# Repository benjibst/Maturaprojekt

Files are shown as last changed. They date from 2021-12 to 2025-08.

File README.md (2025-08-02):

# Maturaprojekt

A machine that uses image processing to find magnetic objects and automatically remove them from an area.

https://github.com/user-attachments/assets/88520221-f3bb-43c3-997b-82101137d2bb

The magnetic objects might look something like this, they are iron washers with a piece of coloured paper attached to them: <br />
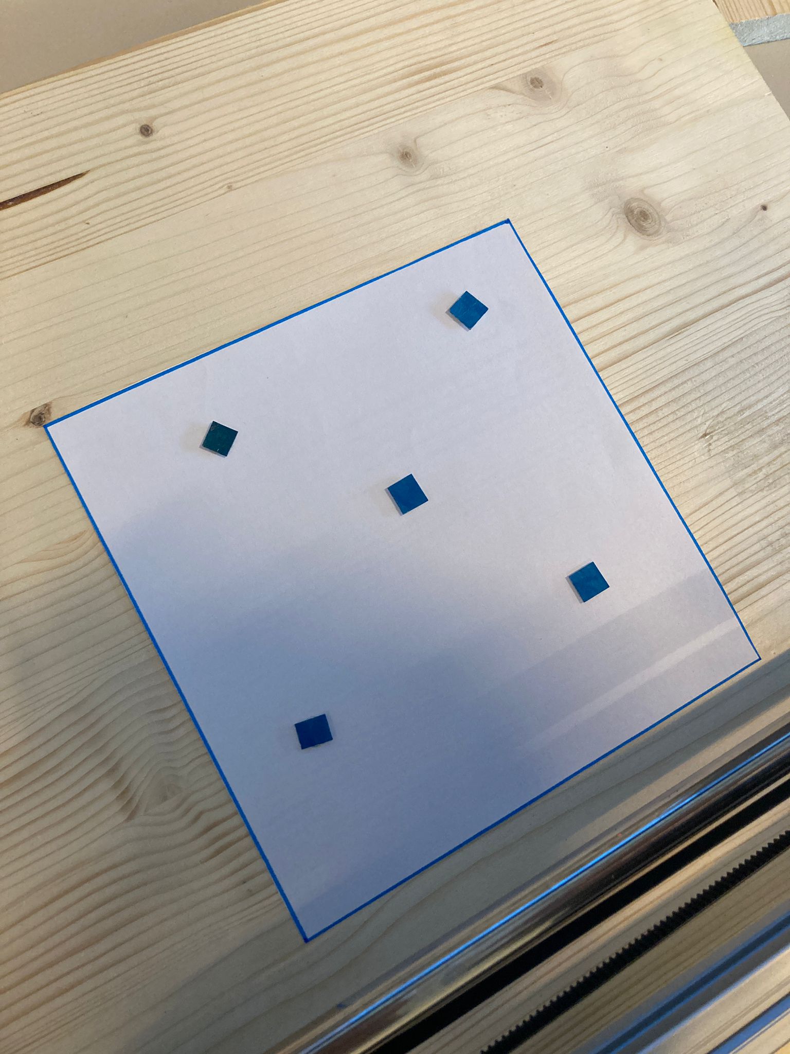
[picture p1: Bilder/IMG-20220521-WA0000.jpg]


First, we use the DroidCam app to send an image of this area to a desktop software I developed, which processes it to find the locations of the objects: <br />
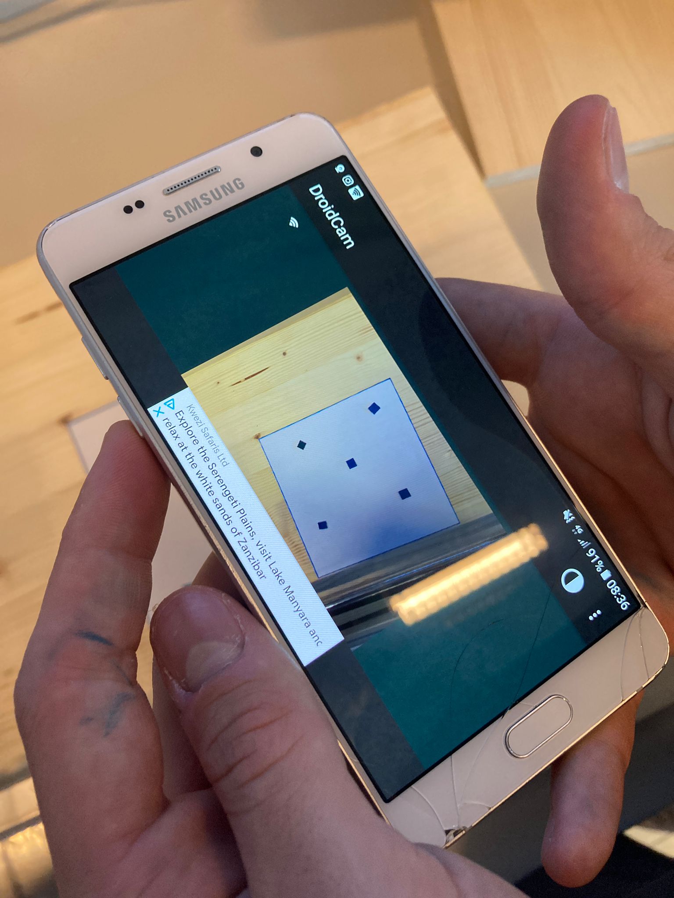
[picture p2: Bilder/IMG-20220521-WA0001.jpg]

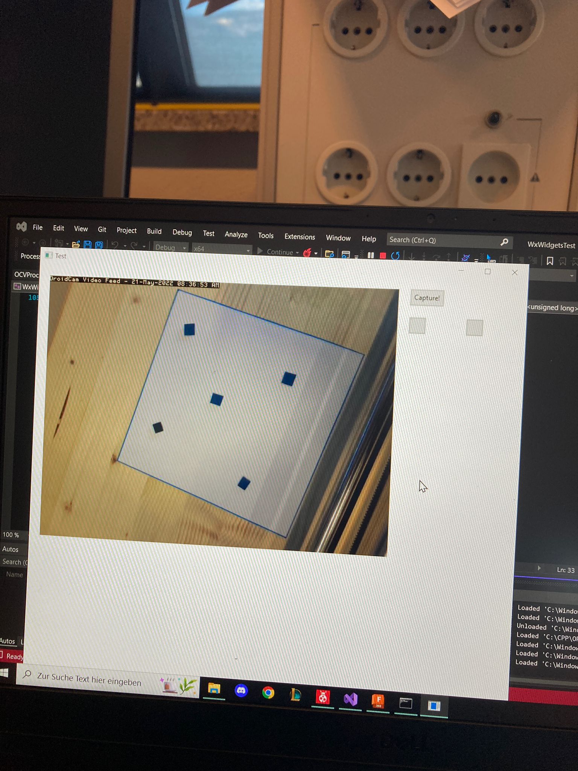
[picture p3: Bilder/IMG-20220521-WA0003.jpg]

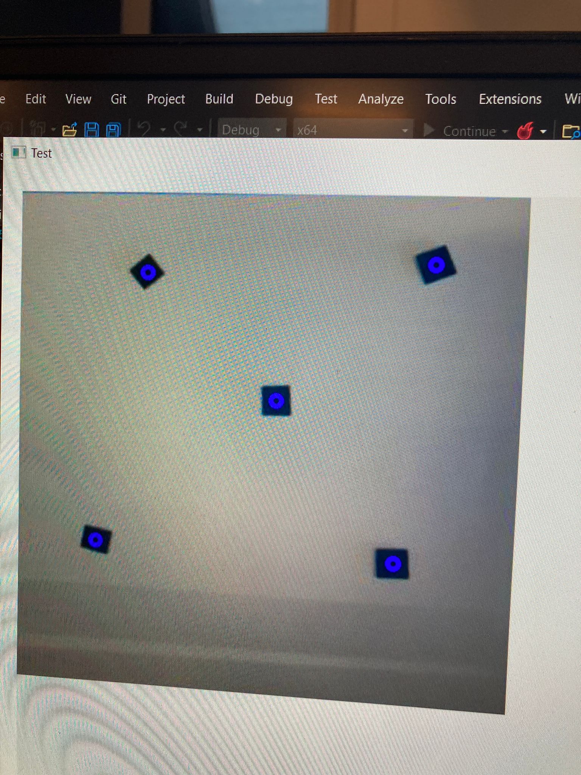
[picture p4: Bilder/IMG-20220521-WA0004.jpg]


The image processing is quite the procedure, but the most important steps can be seen here: <br />
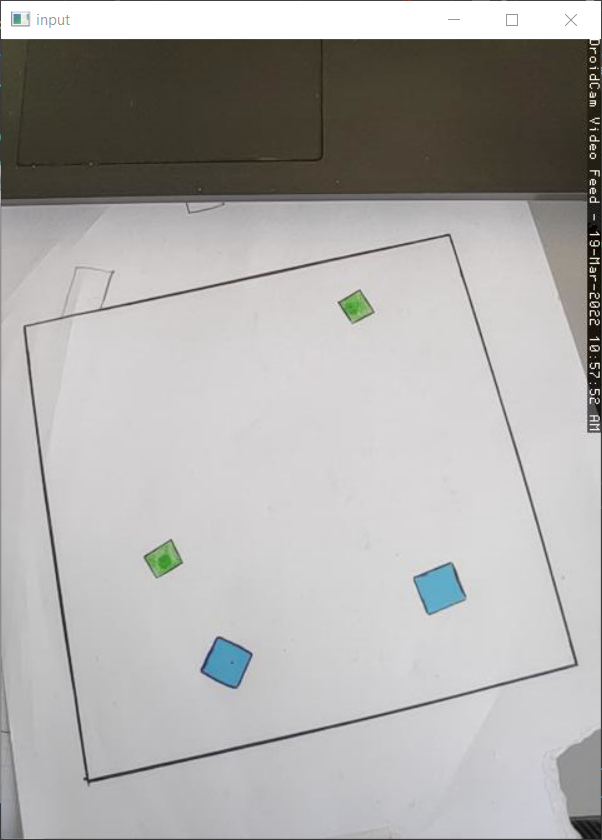
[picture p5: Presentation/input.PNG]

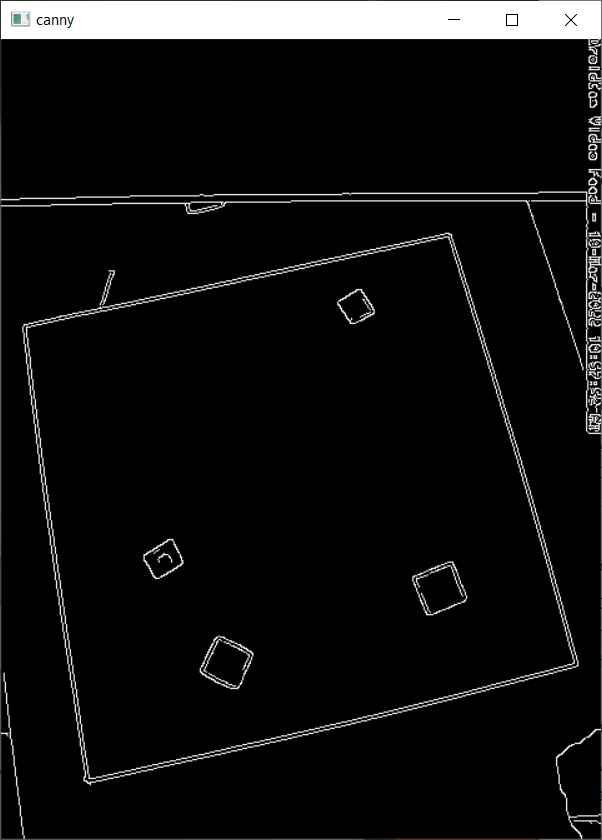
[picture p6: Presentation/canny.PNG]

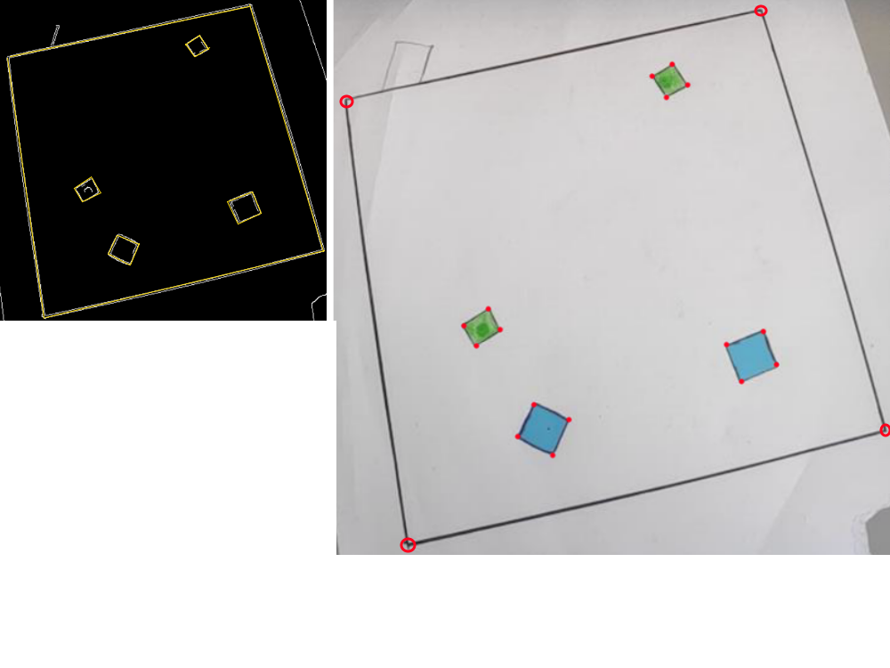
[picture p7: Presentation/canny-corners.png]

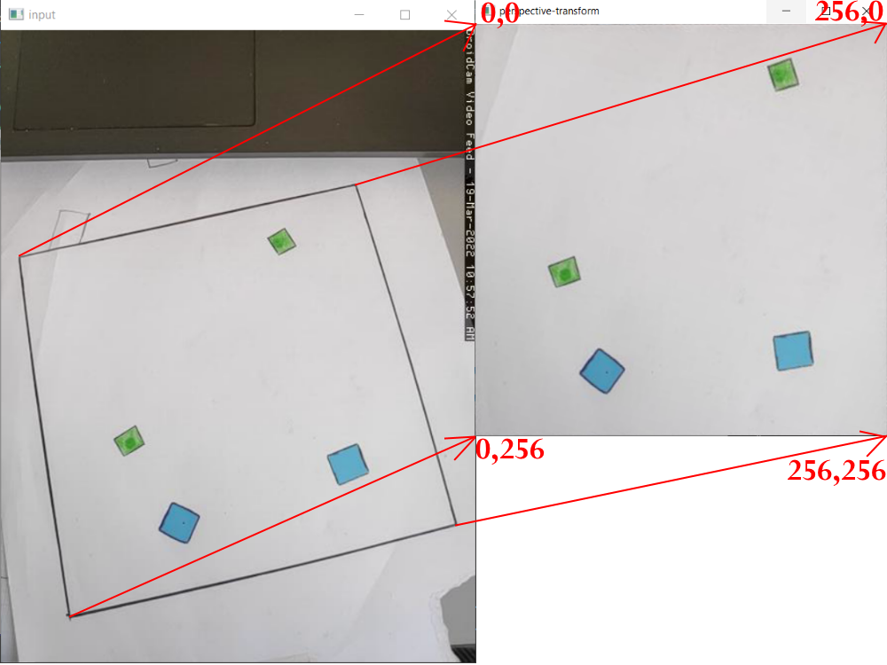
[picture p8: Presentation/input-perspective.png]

<br />

The area that has been found on the image is perspective-transformed into an upright square with side length 256, and the coordinates of the metal objects within this square are sent to a microcontroller. The X and Y coordinates of the objects use 1 byte each, as more precision is unnecessary for a small area like this, and makes data transfer using UART very easy. Upon receiving the coordinates of the objects, the microcontroller (Atmega328p) starts controlling 2 stepper motors to approach each object individually and pick it up using an electromagnet. To achieve this, we built the following machine: <br />
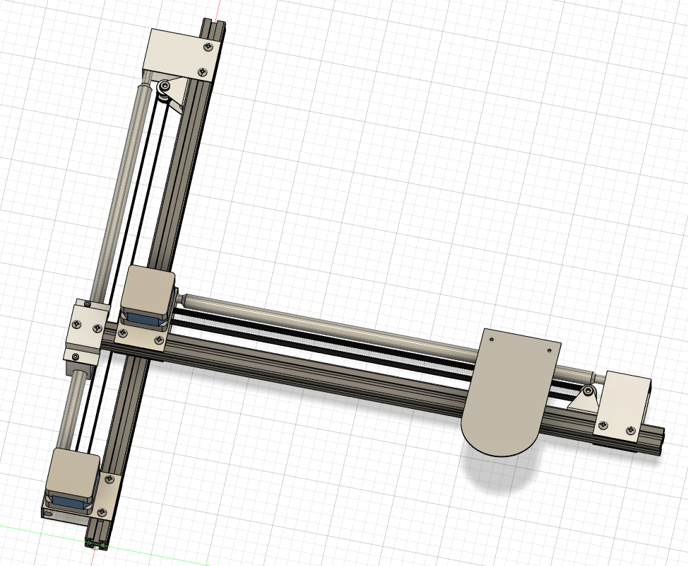
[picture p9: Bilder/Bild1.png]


We made a circuit diagram containing a microcontroller, 2 TMC2226 stepper drivers on custom PCBs that we designed and an electromagnet. Then we designed a PCB for it and ordered it from china: <br /> 
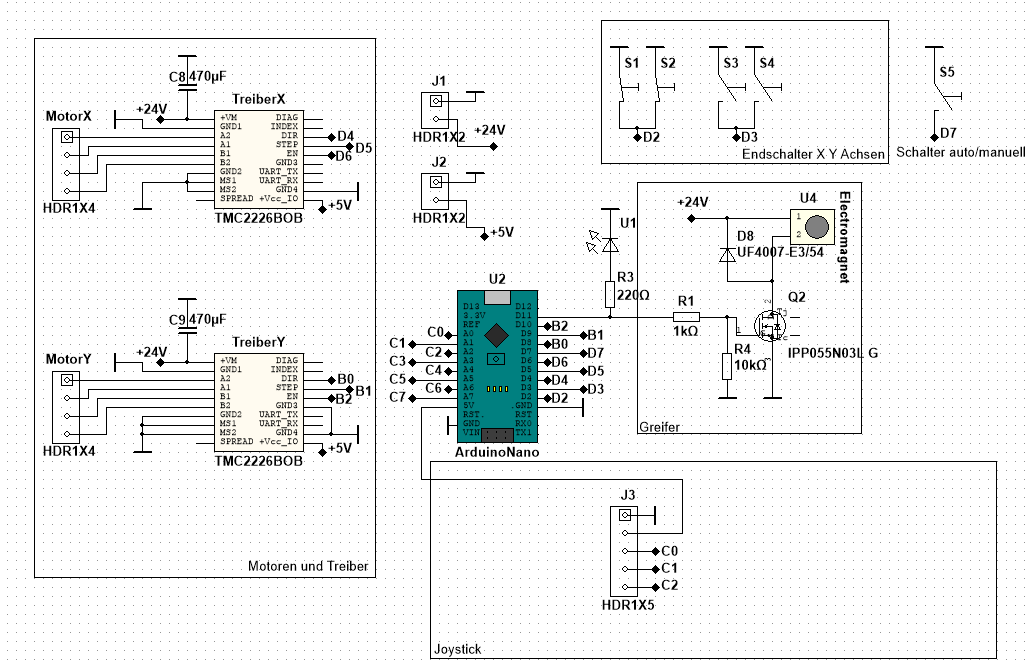
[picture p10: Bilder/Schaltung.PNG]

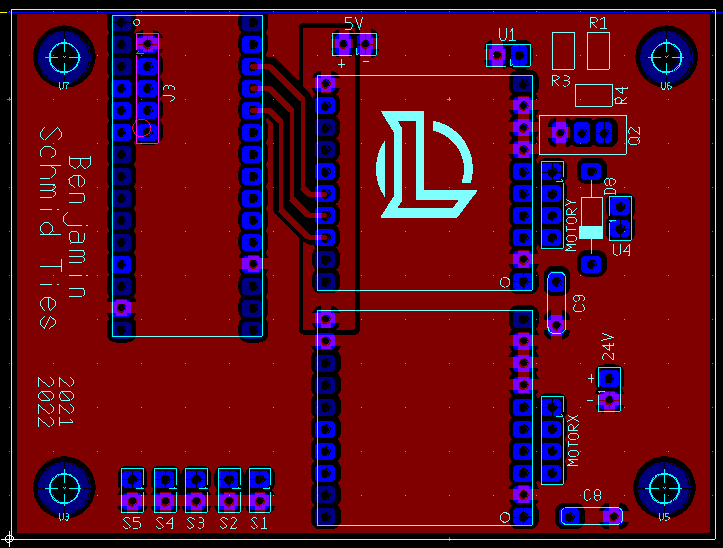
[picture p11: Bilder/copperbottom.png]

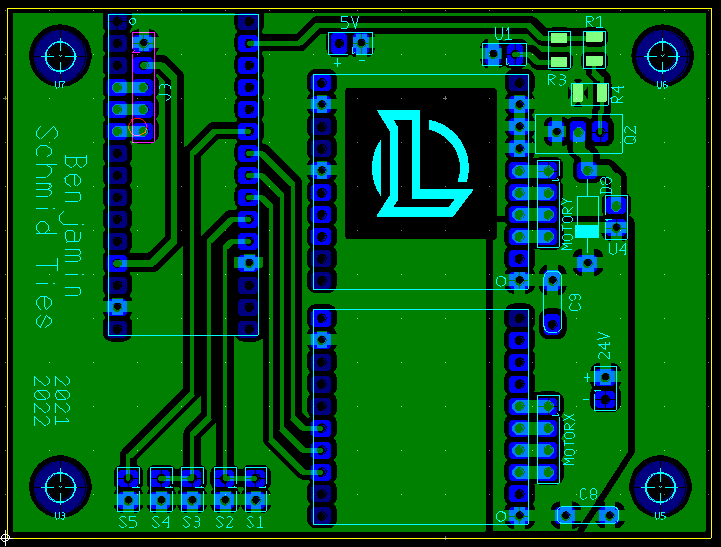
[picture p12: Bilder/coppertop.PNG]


The assembled PCB inside a 3D printed case, together with 2 power supplies and a PC fan: <br />
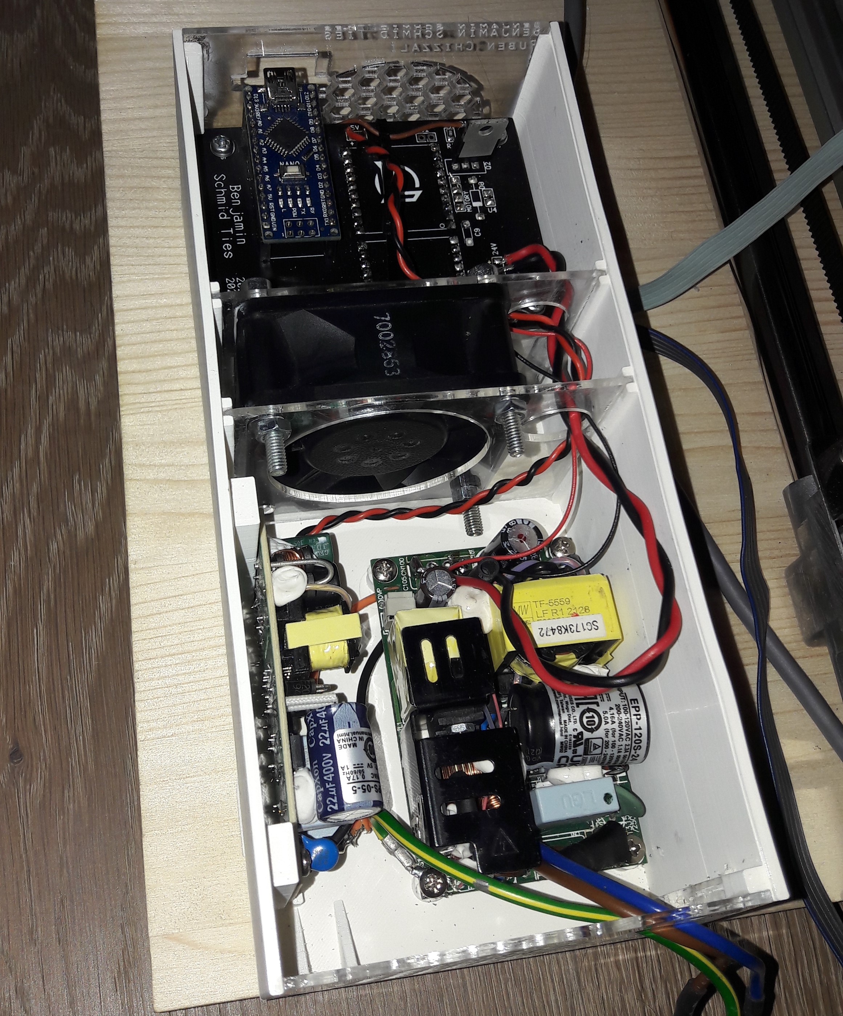
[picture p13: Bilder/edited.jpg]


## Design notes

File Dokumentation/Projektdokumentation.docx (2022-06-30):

Projektdokumentation: Kameragesteuerter Aufräumroboter

Benjamin Schmid Ties, Ruben Chizzali

Einleitung:
Wie werden in der Industrie der Zukunft Maschinen flexibler und kosteneffizienter gesteuert? Die Antwort lautet nicht selten: Bilderkennung. Auch die Firma
Progress Maschinen & Automation AG, bei der ich mein Schulpraktikum absolviert habe, nutzt diese Technik intensiv. Bei meinem Projekt geht es darum, in einem Bild die Koordinaten von metallischen Objekten zu erkennen und diese automatisch wieder an ihren Ursprungsort zuzückzubringen, ohne von einem Menschen gesteuert zu werden, oder wahllos den gesamten Bereich, in dem die Maschine operiert, abzufahren. Die Maschine besteht aus mehreren Bestandteilen, die Hand in Hand arbeiten.

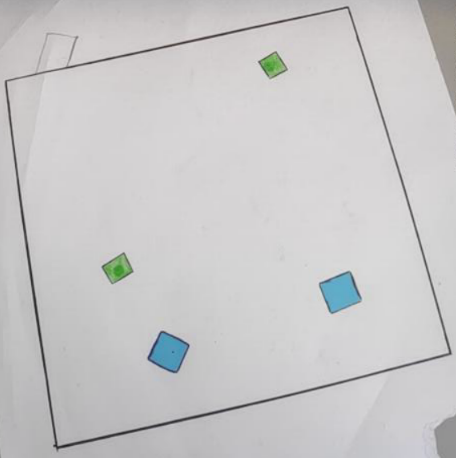
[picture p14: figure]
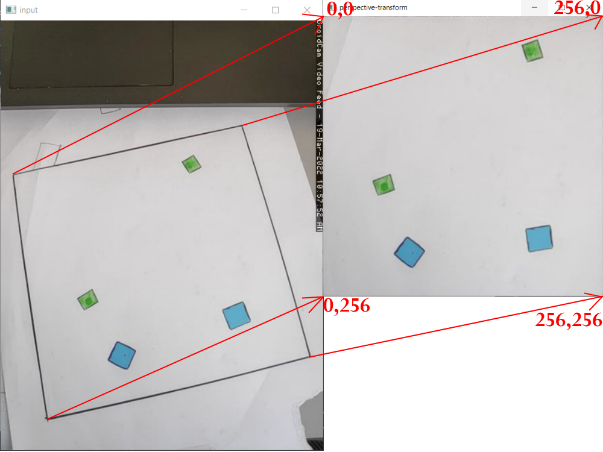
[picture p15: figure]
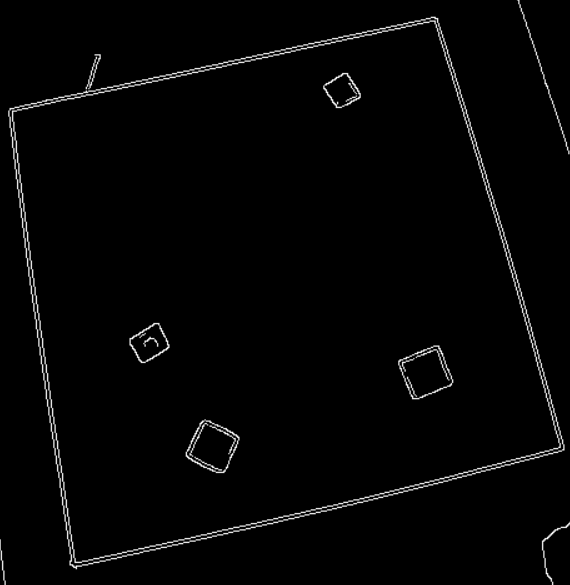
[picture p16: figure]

PC-Software:
Bilderkennung ist zwar für einen Menschen sehr einfach, für einen Computer erfordert sie jedoch viel Rechenleistung. Da ein Microcontroller die nötige Rechenleistung nicht hat, habe ich die Software auf einen PC ausgelagert. In mehreren Schritten wird das aufgenommene Bild verarbeitet, um daraus Informationen zu erlangen. Hier sind nur

die wichtigsten Schritte abgebildet. Zuerst werden auf dem Bild Konturen (abrupte Farbänderungen zwischen benacharten Pixeln) erkannt. Es ergeben sich sehr viele Punkte (hunderte), die mit dem Ramer-Douglas-Peucker-Algorithmus zu Eckpunkten mehrerer Vierecke zusammengefasst werden. Anhand der Eckpunkte aller Vierecke im Bild wird deren Fläche berechnet. Das größte Viereck stellt den Bereich dar, in dem die Maschine operiert. Es wird eine Matrix berechnet, die jeden Punkt im eventuell gedreht und perspektivisch verzerrt fotografierten, größten Viereck des anfänglichen Bildes so transformiert, dass er nun innerhalb eines senkrecht abgebildeten und nicht rotierten Quadrats liegt. Die Mittelpunkte der metallischen Teile, die ebenfalls als Vierecke erkannt werden, werden mit dieser Matrix transformiert und die Koordinaten, die sich ergeben, sind nun die Koordinaten der metallischen Teile relativ zum größten Viereck im Bild. Die Seitenlänge des Quadrats, in dem sie liegen, ist 256, ein Byte. Somit können sie sehr einfach an den Microcontroller über die serielle Schnittstelle geschickt werden.

MCU-Software:
Die Software des Microcontrollers besteht im Wesentlichen daraus, die gesendeten Koordinaten zu empfangen, daraus eine Anzahl an Schritten zu berechnen, die von Schrittmotoren gemacht werden muss, um die Metallteile zu erreichen, und die Schrittmotoren und einen Elektromagneten richtig anzusteuern. Dazu müssen folgende Größen manuell gemessen und im Programm eingetragen werden: der Umfang des Zahnrads der Schrittmotoren, die Größe des Quadrats, in dem sich die Metallteile befinden, und den Abstand des linken unteren Punkts des Quadrats zum 0-Punkt der Maschine. Ein Teil des Programms, bei dem ich lange gebraucht habe, den richtigen Lösungsweg zu finden, war die lineare Beschleunigung der Schrittmotoren. Ich bin auf folgenden Lösungsansatz gekommen: wenn man eine Beschleunigung a wählt (Einheit: Schritte/Sekunde²) und zu jedem Zeitpunkt im Programm die vergangene Zeit t berechnet (über den Zählwert eines vom Systemtakt abhängigen Zählers) kann man die Schritte s, die der Motor bis dahin gemacht haben sollte, berechnen mit s=(a*t²)/2 . Wenn diese Anzahl an Schritten größer ist, als die Schritte die bereits gemacht wurden, wird ein Schritt gemacht. Die Anzahl an Schritten, die zur Beschleunigung verwendet werden, ist konstant. Zum gleichmäßigen Bremsen der Motoren wird der gleiche Ansatz verwendet. Nun wird, um ein Metallteil zu erreichen, das beispielsweise 10000 Schritte in X- und 8000 Schritte in Y-Richtung entfernt liegt, zuerst 2000 Schritte in X Richtung beschleunigt, dann 6000 Schritte mit konstanter Geschwindigkeit zurückgelegt, und anschließend wieder über 2000 Schritte gebremst. In Y-Richtung passiert das Selbe, nur dass hier 4000 Schritte mit konstanter Geschwindigkeit zurückgelegt werden. Danach wird der Elektromagnet eingeschalten und der Weg wird rückwärts gefahren. Am Ende wird der Elektromagnet wieder ausgeschalten. Es gibt auch einen manuellen Modus, in dem man die Motoren mit einem Joystick manuell Steuern und durch Klicken des Joysticks den Elektromagneten an- bzw. ausschalten kann.

Elektronik:
Grundlegend besteht der Schaltplan meines Projekts aus einem Microcontroller (Atmega 328p), 2 Schrittmotoren und den dazugehörigen Treibern, und einem Elektromagneten. Da alternativ zum automatischen Ansteuern der Schrittmotoren auch ein manueller Modus praktisch ist, habe ich einen Joystick vorgesehen, mit dem der Benutzer die Motoren steuern kann. Der Elektromagnet wird durch ein Logik-Mosfet geschalten, und die induzierten Spannungen über eine schnelle Diode kurzgeschlossen. An beiden Achsen sind jeweils Endschalter vorgesehen, um eventuelle Schäden durch Fehler zu vermeiden. Versorgt wird die Schaltung von einem 24V Netzgerät mit 120 Watt und die Logikspannung der Treiber wird durch ein 5V Netzgerät zur Verfügung gestellt. Die elektrische Beschaltung der Schrittmotor-Treiber wurde von Ruben Chizzali geplant und wir haben die Platinen der Treiber professionell anfertigen lassen (JLC-PCB).

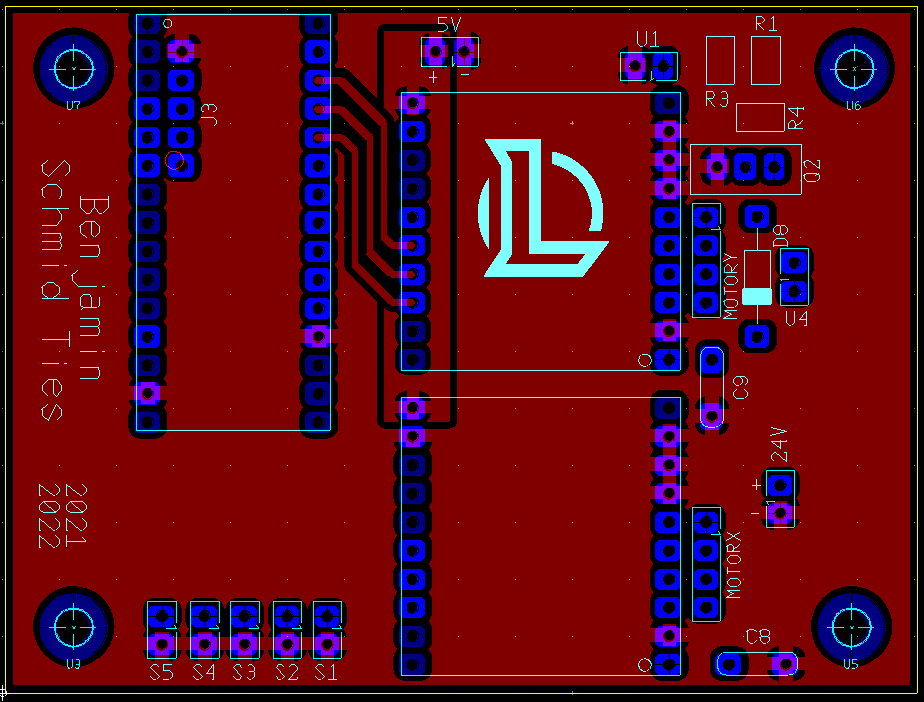
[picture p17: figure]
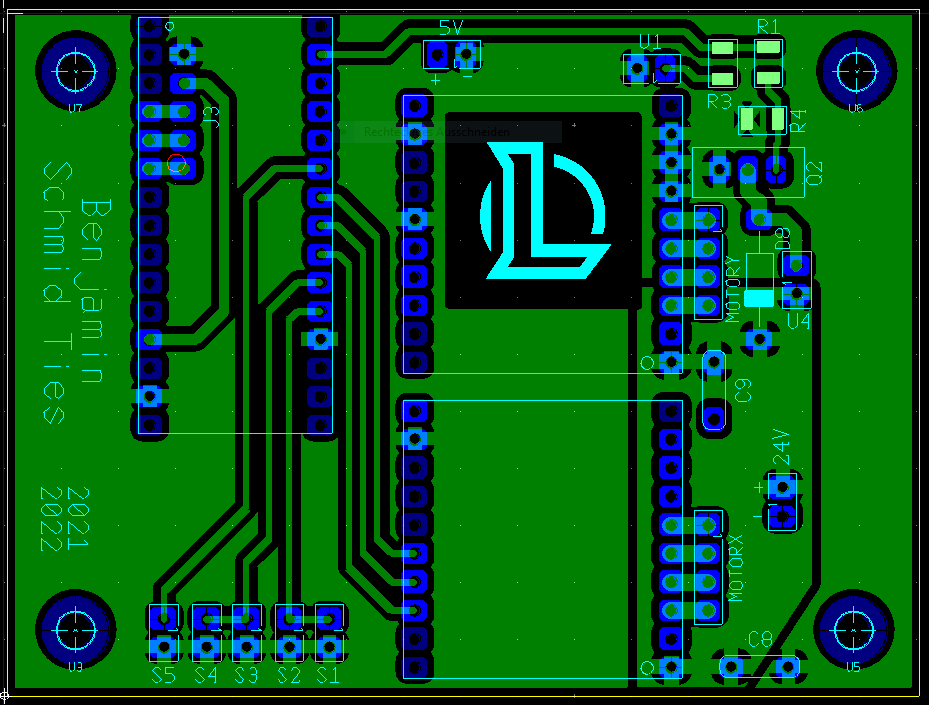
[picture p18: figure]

Schaltplan

Layout (Copper top) Layout (Copper bottom)

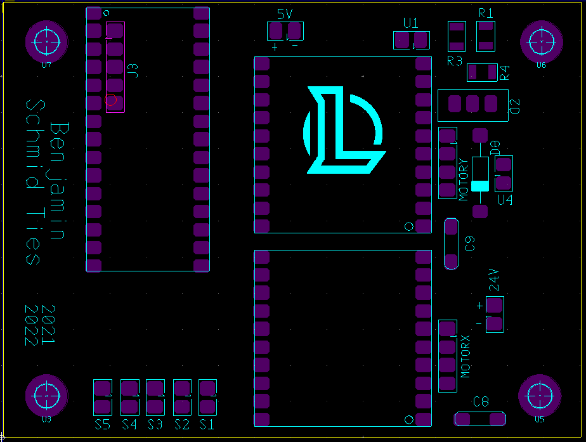
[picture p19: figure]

Für die Schaltung habe ich ein Platinen-Layout mit Ultiboard entworfen und anfertigen lassen. Die Platine ist zweilagig und beinhaltet weibliche Header-Pins zum Verbinden des Arduino Nano und der Schrittmotor-Treib/er Platinen.

Bestückungsplan

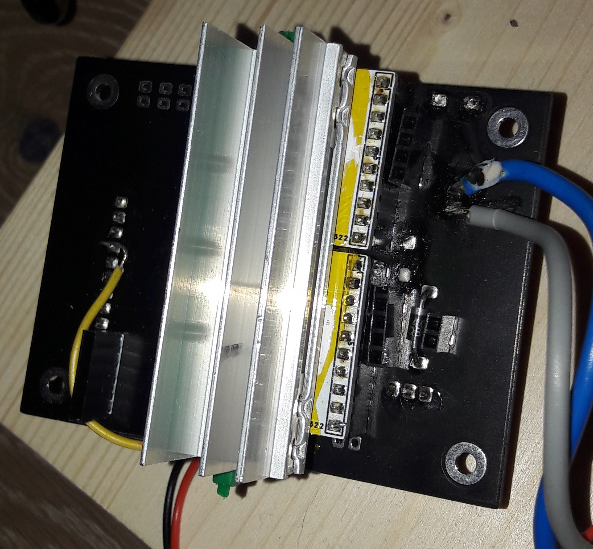
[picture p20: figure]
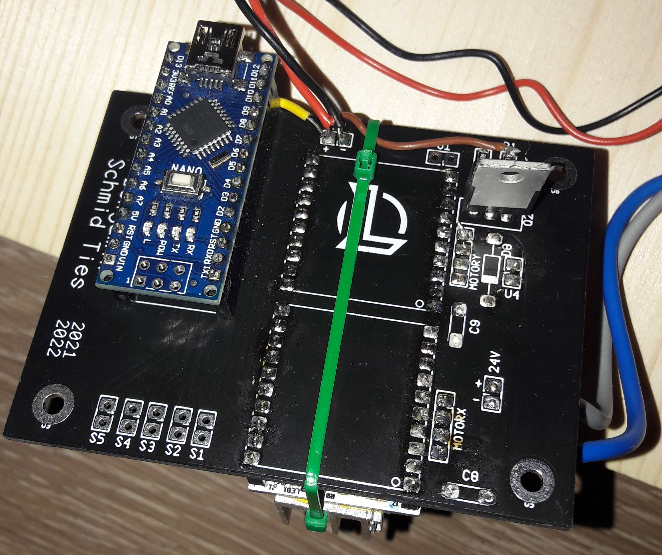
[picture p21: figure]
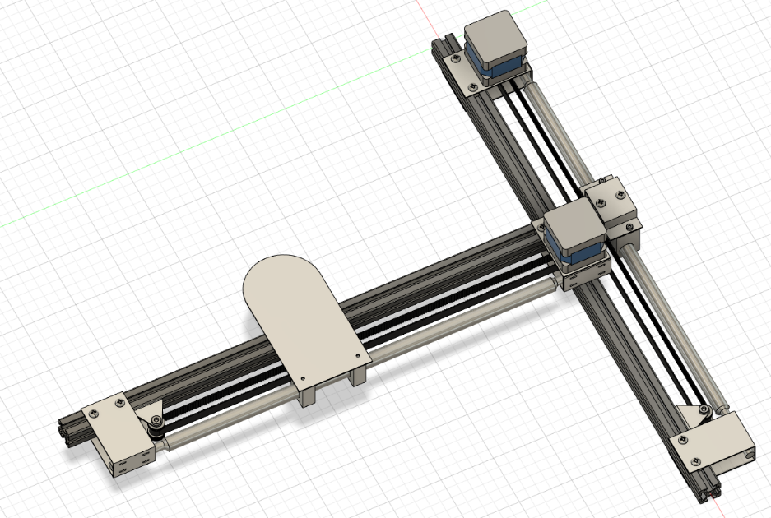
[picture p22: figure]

Mechanischer Aufbau:

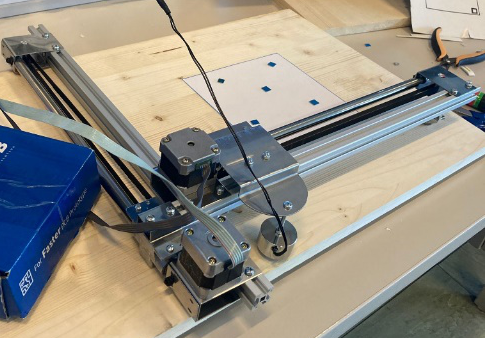
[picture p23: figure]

Um die Maschine zu bauen haben wir Führungen, Motoren, Gleitlager und Riemen aus einem kaputten Drucker recycelt. Ruben Chizzali hat einen 3D-Plan in Fusion-360 konstruiert, und wir haben uns beim Aufbau danach gerichtet. Das Grundgerüst besteht aus Aluminium-Profilen, die über Inox Bleche miteinander verbunden sind und an denen mit Blechen die Führungen und Riemen angebracht sind. Am Ende der X-Achse befindet sich ein Rad. Auch die Platte, an
der der Elektromagnet angebracht ist, hat ein Rad, damit sie auf dem Aluprofil rollt.

Benjamin Schmid Ties5AutB29.05.2022

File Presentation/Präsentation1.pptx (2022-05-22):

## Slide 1

## Preparing image for processing

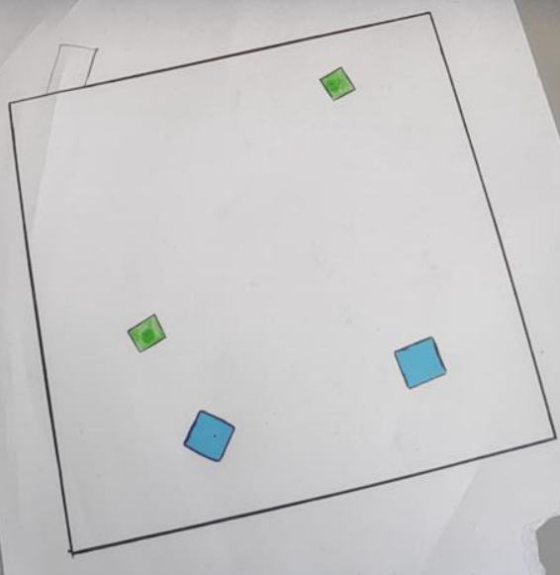
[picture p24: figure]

Input image

Grayscale

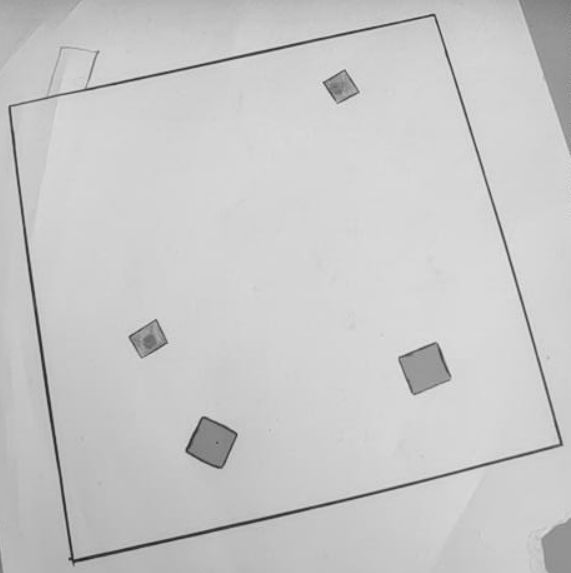
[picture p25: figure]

Gaussian blur

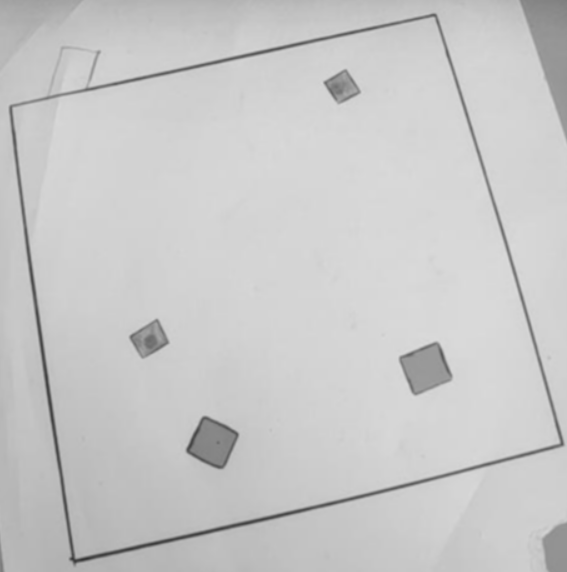
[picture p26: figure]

## Canny edge detector

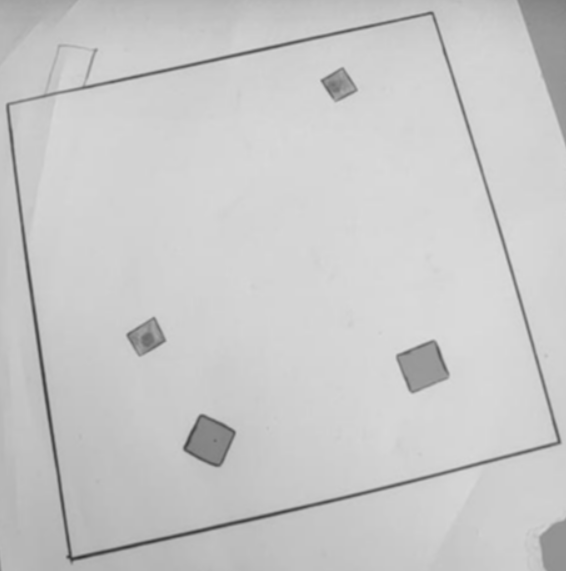
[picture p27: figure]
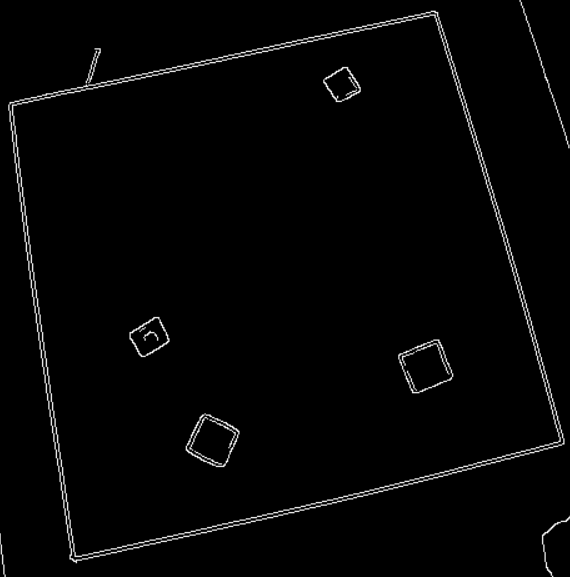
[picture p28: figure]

## Polygon approximation


Ramer-Douglas-Peucker algorithm

Curve consisting of line segments→similar
curve with fewer points

## Perspective transformation


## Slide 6

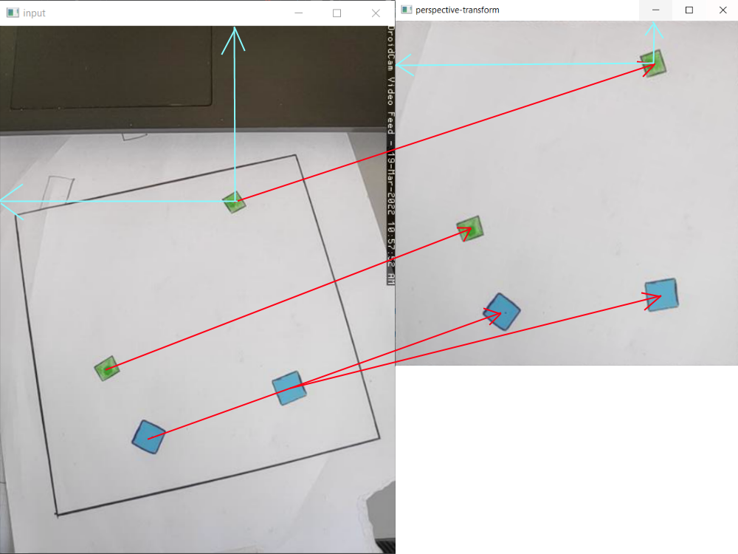
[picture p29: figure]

- Transform center points of squares
- 1 Byte for X and Y coordinates
- Easy data transfer to MCU

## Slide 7

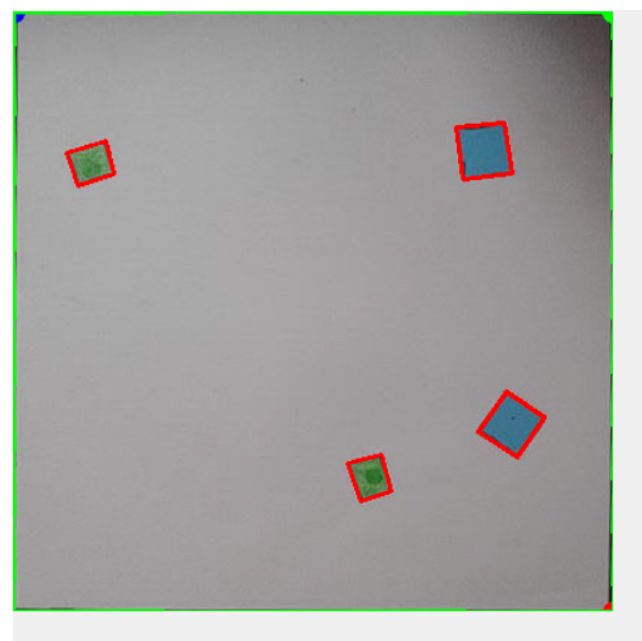
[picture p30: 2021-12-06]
Example_transformed.PNG

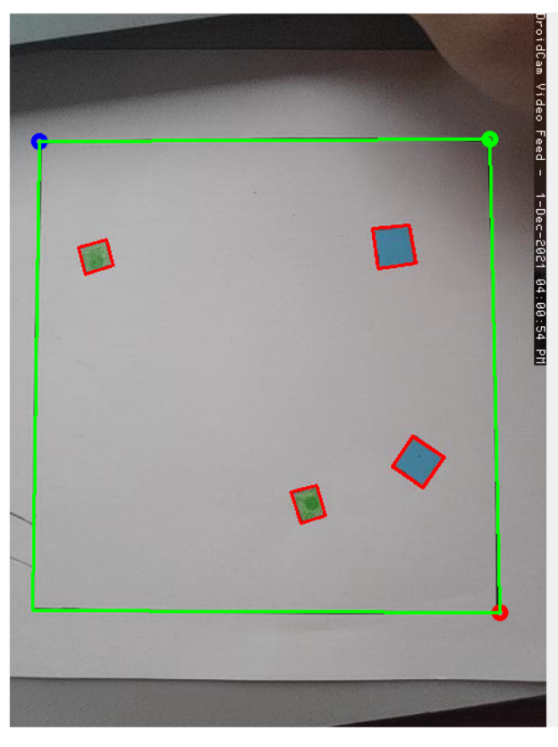
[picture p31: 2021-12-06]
Example.PNG

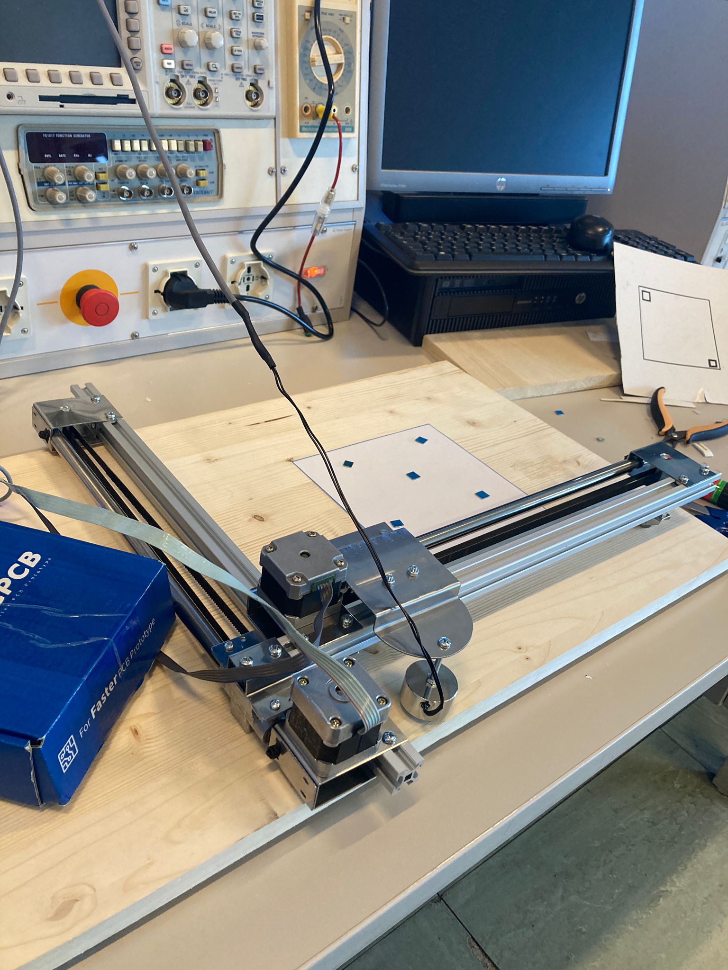
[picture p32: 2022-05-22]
Bilder/IMG-20220521-WA0002.jpg

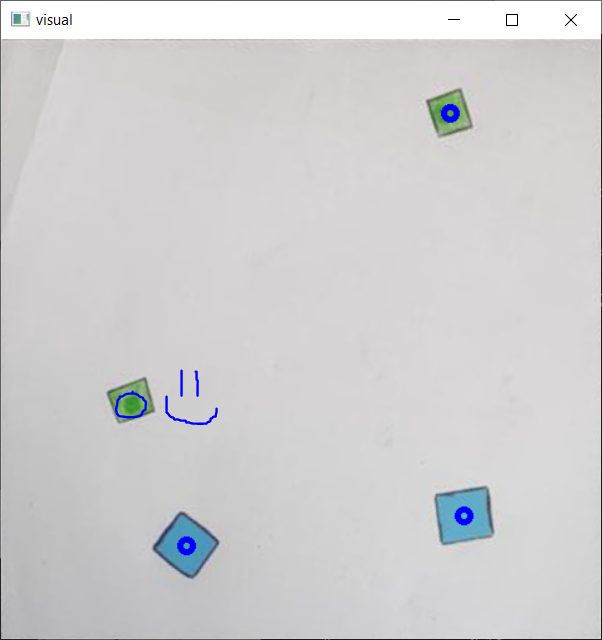
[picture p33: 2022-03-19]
Presentation/visual.PNG

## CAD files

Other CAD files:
3D/3DBlech/PlatteConn_1.ipt
3D/3DBlech/PlatteMagnet_1.ipt
3D/3DBlech/PlatteMotor_2.ipt
3D/3DBlech/PlatteOben_2.ipt
3D/3DBlech/PlatteRad_2.ipt
3D/3DBlech/PlatteUnten_4.ipt
3D/Case/24V.ipt
3D/Case/5V.ipt
3D/Case/OldVersions/Platine.0001.ipt
3D/Case/Platine.ipt

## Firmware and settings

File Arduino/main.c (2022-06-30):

#include <avr/io.h>
#include <avr/interrupt.h>
#include "UART.h"
#include "defines.h"
#include "stepper.h"
#include <stdlib.h>
#include <stdbool.h>

char strcoords[20]; //21 byte für anzahl der punkte und 2 byte pro punkt mit max. 10 punkte
target targets[10];
uint8_t targetcnt=0;
uint8_t pointsreceived = 0;
steptypes man_dirx;
steptypes man_diry;
char stringx[7];
char stringy[7];
uint8_t mode=1;
bool manMode = true;
bool autoMode = false;
//LED PB5

void init_adc();
uint8_t read_adc(uint8_t pinmsk);
void commonSetup();
void initManMode();
void autoModeCollectPoints();
void stopManMode();

ISR(USART_RX_vect)
{
	uint8_t sreg = SREG;
	SREG&=~(1<<7);
	unsigned char cmd = _getch();
	if(cmd == 'm')
	{
		
		PORTB |=1<<5;
		initManMode();
		manMode = true;
		autoMode = false;
	}
	else if(cmd == 'a')
	{
		
		PORTB &=~(1<<5);
		stopManMode();
		autoMode = true;
		manMode = false;
	}
	else if(cmd < 10 &&cmd >=0 && autoMode)
	{
		targetcnt = cmd;
		PORTB|=1<<5;
		uint8_t i;
		for(i=0;i<2*cmd;i++)
			strcoords[i]=_getch();
		for(i=0;i<targetcnt;i++)
		{
			targets[i].x=strcoords[2*i];
			targets[i].y=strcoords[2*i+1];
			targets[i].pos=pointfrompos(targets[i].x,targets[i].y);
		}
		autoModeCollectPoints();
	}
	SREG = sreg;
}
ISR(TIMER0_OVF_vect)
{
	uint8_t sreg = SREG;
	cli();
	int8_t target_xvel = read_adc(0)-128;
	int8_t target_yvel = read_adc(1)-128;
	
	if(abs(target_xvel)<3)
		target_xvel=0;
	if(abs(target_yvel)<3)
		target_yvel=0;
	
	if(target_xvel>0)
		man_dirx  = XGO;
	else 
		man_dirx = XCOME;
	if(target_yvel>0)
		man_diry  = YGO;
	else
		man_diry = YCOME;
		
	float target_xfreq = (pow(2,abs(target_xvel)/28.0f)-1)*300.0f;
	float target_yfreq = (pow(2,abs(target_yvel)/28.0f)-1)*300.0f;
	
	uint16_t ocrx_target=(uint16_t)15625/target_xfreq;
	uint16_t ocry_target=(uint16_t)15625/target_yfreq;
	uint8_t ocrx = ocrx_target<=255?ocrx_target:255;
	uint8_t ocry = ocry_target<=255?ocry_target:255;
	
	
	if(target_xvel==0)
		TCCR1B&=0b11111000;
	else
	{
		OCR1AL=ocrx;
		OCR1AH=0;
		if(TCNT1>ocrx)
			TCNT1 = ocrx -1;
		TCCR1B|=0b101;
	}
	if(target_yvel==0)
		TCCR2B&=0b11111000;
	else
	{
		OCR2A=ocry;
		if(TCNT2>ocry)
			TCNT2 = ocry-1;
		TCCR2B|=0b111;
	}
	SREG = sreg;
}
ISR(TIMER1_COMPA_vect) //stepper x routine
{
	uint8_t sreg = SREG;
	cli();
	step(man_dirx);
	SREG = sreg;
}
ISR(TIMER2_COMPA_vect) //stepper y routine
{
	uint8_t sreg = SREG;
	cli();
	step(man_diry);
	SREG = sreg;
}

int main(void)
{
	commonSetup();
		
		uint8_t portc_old;
		uint8_t portc_now;
		while(1)
		{
			while (manMode)
			{
				portc_now = !(PINC&(1<<JOYSTICK_SW));
				if(portc_now&&!portc_old)
				{
					PORTB^=1<<5;
					PORTB ^= (1<<MAGNET_PIN);
					_delay_ms(5);
				}
				portc_old=portc_now;
			}
		}
}
void init_adc()
{
	ADCSRA=0x87;
	ADMUX=0x60;
}
uint8_t read_adc(uint8_t pinmsk)
{
	ADMUX &= ~ (0b1111);
	ADMUX |= pinmsk;
	ADCSRA|=(1<<ADSC);
	while(ADCSRA&(1<<ADSC));
	return ADCH;
}

void commonSetup()
{
	DDRC=0; //joystick port as input
	PORTC|=1<<JOYSTICK_SW; //enable pull up
	DDRD=
	(1<<XDirPin)|
	(1<<XStepPin)|
	(1<<XEnPin); //stepper pins as output
	
	DDRB =
	(1<<MAGNET_PIN)|
	(1<<YDirPin)|
	(1<<YStepPin)|
	(1<<YEnPin); //stepper pins and magnet output pins
	DDRB |=1<<5; //builtin led
	
	
	init_usart9600();
	
	SREG|=(1<<7);
}

void initManMode()
{
	init_adc();
	__asm__ volatile ("sei");
	TCCR0A = 0;
	TCCR0B = 0b101; //prescaler 1/1024
	TIMSK0 |=1<<TOIE0;
	
	TCCR1A = 0;
	TCCR1B = (1<<WGM12);
	TIMSK1 = (1<<OCIE1A);
	TCCR2A = 1<<WGM21;
	TCCR2B=0;
	TIMSK2 =1<<OCIE2A;
}
void stopManMode()
{
	ADCSRA &= ~ 0x87;
	ADMUX &= ~0x60;
	TCCR0B = 0;
	TCCR1B = 0;
	TIMSK1 = 0;
	TCCR2A = 0;
	TIMSK2 = 0;
}
void autoModeCollectPoints()
{
	cli();
	for(uint8_t i=0;i<targetcnt;i++)
	{
		
		PORTB |=1<<5;
		move(XGO,targets[i].pos.x);
		move(YGO,targets[i].pos.y);
		PORTB|=(1<<MAGNET_PIN);
		_delay_ms(200);
		
		PORTB &=~(1<<5);
		move(YCOME,targets[i].pos.y);
		move(XCOME,targets[i].pos.x);
		PORTB&=~(1<<MAGNET_PIN);
		
	}
	
}

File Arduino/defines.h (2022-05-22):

#pragma  once
#define FIELD_SX 170 //Field dimensions in mm
#define FIELD_SY 170
#define OFFSETX 80	//Vector to the bottom left corner of the field in mm
#define OFFSETY 100
#define ACCEL 1400
#define MICROSTEPS 8
#define STEPSTURN 400
#define JOYSTICK_SW 2
#define MAGNET_PIN 4
typedef struct
{
	uint16_t x;
	uint16_t y;
} point;

typedef struct
{
	uint8_t x;
	uint8_t y;
	point pos;
}target;

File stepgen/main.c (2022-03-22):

#include <stdio.h>
#include <stdlib.h>

int main()
{

    FILE* outputfile;
    int accelsteps=0,vend=0,freq=0,timerafter=0;
    double zeit=0,accel=0;

    printf("Anzahl der Schritte während der Beschleunigung: ");
    scanf("%i",&accelsteps);
    int steps[accelsteps];

    printf("\nGeschwindigkeit nach der Beschleunigung: ");
    scanf("%i",&vend);

    printf("\nTimer Frequenz: ");
    scanf("%i",&freq);

    zeit=2.0*accelsteps/vend;
    accel=(vend*vend)/(2*accelsteps);
    printf("%f\n",accel);
    timerafter=zeit*freq+1;

    int laststeps=0;
    int currentsteps=0;
    int j=0;
    for(int i=1;i<=timerafter;i++)
    {
        currentsteps=accel*(i/(float)freq)*(i/(float)freq)/2;
        if(currentsteps>laststeps)
        {
            steps[j++]=i;
            laststeps=currentsteps;
            printf("%i\n",i);
        }

    }
    outputfile=fopen("output.txt","w+");
    for(int i=0;i<accelsteps/10;i++)
    {
        for(int j = i*10;j<10*i+10;j++)
        {
            fprintf(outputfile,"%i, ",steps[j]);
        }
        fputs("\n",outputfile);
    }
    fclose(outputfile);
    system("pause");
}

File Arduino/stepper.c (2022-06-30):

#include "stepper.h"

inline void step(steptypes s)
{
	XPort&=~(1<<XDirPin);		//set dir pins to 0
	YPort&=~(1<<YDirPin);
	XPort|=((s>>1)&1)<<(XDirPin); //if dir bit is set set dir bits in stepper
	YPort|=((s>>1)&1)<<(YDirPin);
	XPort^=((~s)&1)<<XStepPin; //if stepper bit is 0 then do step x 
	YPort^=(s&1)<<YStepPin;	//if stepper bit is 1 then do step y
}

point pointfrompos(uint8_t x,uint8_t y)
{
	uint16_t microstepsturn=STEPSTURN*MICROSTEPS;
	
	return (point){
		(uint16_t)(x/255.0f*FIELD_SX+OFFSETX)/42.25*microstepsturn,
		(uint16_t)(y/255.0f*FIELD_SY+OFFSETY)/42.25*microstepsturn};
}
void move(steptypes s,uint16_t microsteps)
{
	TCCR1A = 0;
	TCCR1B=0b00001100;
	uint16_t donesteps=0;
	uint16_t sollsteps=0;
	uint16_t accelsteps=1200;
	uint16_t tcntrev=0;
	microsteps -= 2*accelsteps;
	float time;
	float vend;
	TCNT1=0;
	while(donesteps<=accelsteps)
	{
		time = TCNT1/15625.0;
		sollsteps=ACCEL*time*time;
		sollsteps>>=1;
		if(sollsteps>donesteps)
		{
			donesteps++;
			step(s);
		}
	}
	tcntrev=TCNT1;
	TCNT1=0;
	vend=(uint16_t)15625.0/(ACCEL*time);
	while(microsteps--)
	{
		while(TCNT1<vend);
		TCNT1=0;
		step(s);		
	}
	TCNT1=0;
	while(donesteps>0)
	{
		
		time = (tcntrev-TCNT1)/15625.0;
		sollsteps=ACCEL*time*time;
		sollsteps>>=1;
		if(sollsteps<donesteps)
		{
			donesteps--;
			step(s);
		}
	}
}

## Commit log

2021-08-13 select device in dialog
2021-08-14 button capture
2021-08-15 capture frame
2021-09-10 opencv camera stream to DC
2021-09-15 add image processing to button
2021-11-12 fix rotation button fix rotation stretchdibits refactoring
2022-01-17 add LCD
    [Bauteile_SchmidTies.xlsx]
2022-01-23 minor UART lib changes
2022-02-23 schaltung und layout
    [calc.xlsx]
2022-03-16 drill mount holes
    [Layout - Board Outline.gbr, Layout - Copper Bottom.gbr, Layout - Copper Top-Copper Bottom.drl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]
2022-03-17 stepgen for linear stepper acceleration
    [calc.xlsx]
2022-03-19 presentation and linear accel
    [Layout - Board Outline.gbr, Layout - Copper Bottom.gbr, Layout - Copper Top-Copper Bottom.drl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]
2022-03-22 move stepper in direction n microsteps
    [Magnet-Klauber v4.f3z]
2022-03-23 control xy stepper
2022-04-02 inventor drawings
    [Magnet-Klauber v4.f3z, Platte1.0002.ipt, Platte1_1.0003.ipt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]
2022-04-10 3d inventor
    [Platte1.0002.ipt, Platte1_1.0003.ipt, Platte1_1.ipt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]
2022-05-02 3d drawings folder structure
    [24V.ipt, 5V.ipt, Platine.0001.ipt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]
2022-05-12 debug arduino application
2022-05-18 fix man mode working now
    [main.c]
2022-05-18 control magnet
2022-07-01 case image
2023-01-08 images of schematic and pcb
